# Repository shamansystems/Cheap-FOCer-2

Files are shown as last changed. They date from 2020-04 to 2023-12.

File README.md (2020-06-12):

# Cheap FOCer 2 (v0.9)

Low-Cost(around $120 for 5 boards and components) Motor Controller based on the VESC 6

Front and Back:

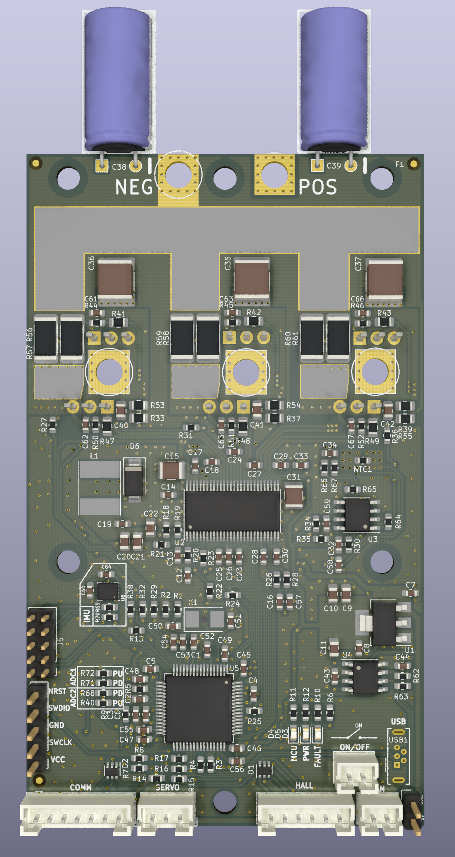
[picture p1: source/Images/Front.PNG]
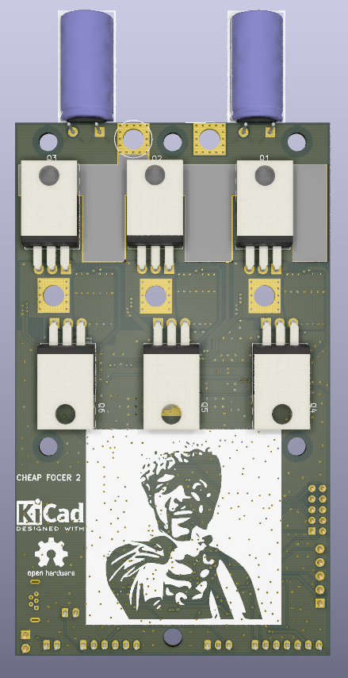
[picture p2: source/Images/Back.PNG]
 

Pin outs:
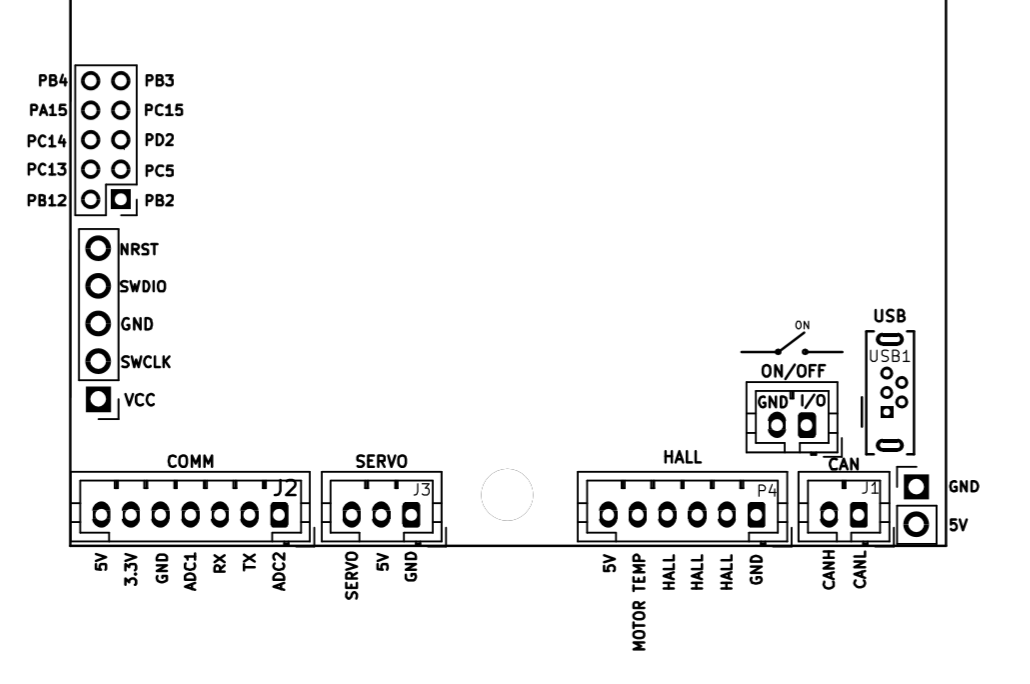
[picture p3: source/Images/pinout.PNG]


## [Support Thread](https://forum.esk8.news/t/cheap-focer-2-open-source-low-cost-vesc-6-based-esc-prototyped-materials-arrived-for-test-batch/13631/1)

## Guides

* [Ordering Guide](./guides/ordering/readme.md)
* [Assembly Guide](./guides/assembly/readme.md)

## Capabilities

* 35A continuous and 70A peak with good heat sinking. These are real values. Not marketing numbers

* Up to 50.4V(12s) safe operating voltage.  For 20s version take a look at [these FOCers](https://forum.esk8.news/t/some-new-focers-84v-vesc-6-based-controllers/1513).

* Compatible with the VESC Tool for configuration

* Open source enclosure design to come

* “Living” LCSC BOM to come. BOM document to be continuously updated with compatible and stocked components from LCSC

## Advantages over VESC 6

* Significantly lower build and BOM cost

* TO-220 FETs allow for big heat sink attachment for better thermal performance

* 2-layer PCB that enables low-cost manufacturing from JLCPCB

* Designed with JLCPCB’s SMT assembly service in mind

* Added optional ON/OFF connector to turn off control circuitry when controller is not in use

* CAN connector changed to 2-pin to avoid improper connections that can cause damage

* ESD protected I/O

* Hardware open sourced

* Designed with direct meme integration

## Advantages over Cheap FOCer 1

* VESC 6 based instead of VESC 4.12

* Significantly improved layout to reduce current loops and facilitate low-noise operation of both the power stage and control circuitry for more stable operation

* Has IMU for balancing applications

* Lower profile

* Handles lower inductance motors much better

* All components on the top side except MOSFETs

* Addition of JST connectors to replace pin headers for Servo, CAN, COMM, ect.

* Addition of header for unused GPIO pins

* Micro USB

## Disadvantages (that I know of)

* Larger than original VESC 6. Cheap FOCer 2 is about 60mm x 100mm x 14mm without enclosure/heat sink

* Uses custom firmware that’s not currently supported in the VESC project. Will make firmware available on GitHub until Cheap FOCer 2 is added to and supported by the official VESC project.

## Kown Issues

* :warning: **Potential Issue with SMT Assembly of the DRV8301 from JLCPCB**

A few have reported blown up D1 diode arrays upon initial powering on of the CFOC2. The issue has been discovered to be inadequate soldering of the DRV which leads to an unregulated 5V of which could actually be 7V or greater. This doesn't happen with every unit and seems to be intermittent. 

**It is recommended that you reflow the DRV and/or touch up the soldering of both the legs and the large pad underneath before initial power on.**

The potential cause of this is the small hole in the DRV's ground pad that was meant to allow soldering of the DRV with even a normal iron (like the CFOC1). This will be removed in the CFOC2 v1.0 release and the pad returned to a normal SMD pad. 

## Warning

* The Cheap FOCer 2 has been bench tested but is still being field tested. Hardware or firmware flaws could still exist and affect user operation.
* You are liable for any and all controllers built using this design. This product is intended for hobbyists and not intended for commercial use.

## License

Cheap FOCer 2 is licensed under the Creative Commons Attribution-ShareAlike 4.0 International License. To view a copy of this license, visit <http://creativecommons.org/licenses/by-sa/4.0/.>

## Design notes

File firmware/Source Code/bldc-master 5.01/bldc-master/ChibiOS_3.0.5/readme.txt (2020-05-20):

*****************************************************************************
*** Files Organization                                                    ***
*****************************************************************************

--{root}                  - ChibiOS/RT directory.
  +--readme.txt           - This file.
  +--documentation.html   - Shortcut to the web documentation page.
  +--license.txt          - GPL license text.
  +--exception.txt        - GPL exception text (stable releases only).
  +--demos/               - Demo projects, one directory per platform.
  +--docs/                - Documentation.
  |  +--common/           - Documentation common build resources.
  |  +--hal/              - Builders for HAL.
  |  |  +--Doxyfile_*     - Doxygen project files (required for rebuild).
  |  |  +--html/          - Local HTML documentation (after rebuild).
  |  |  +--reports/       - Test reports.
  |  |  +--rsc/           - Documentation resource files (required for rebuild).
  |  |  +--src/           - Documentation source files (required for rebuild).
  |  |  +--Doxyfile_*     - Doxygen project files (required for rebuild).
  |  |  +--index.html     - Local documentation access (after rebuild).
  |  +--nil/              - Builders for NIL.
  |  |  +--Doxyfile_*     - Doxygen project files (required for rebuild).
  |  |  +--html/          - Local HTML documentation (after rebuild).
  |  |  +--reports/       - Test reports.
  |  |  +--rsc/           - Documentation resource files (required for rebuild).
  |  |  +--src/           - Documentation source files (required for rebuild).
  |  |  +--Doxyfile_*     - Doxygen project files (required for rebuild).
  |  |  +--index.html     - Local documentation access (after rebuild).
  |  +--rt/               - Builders for RT.
  |  |  +--html/          - Local HTML documentation (after rebuild).
  |  |  +--reports/       - Test reports.
  |  |  +--rsc/           - Documentation resource files (required for rebuild).
  |  |  +--src/           - Documentation source files (required for rebuild).
  |  |  +--Doxyfile_*     - Doxygen project files (required for rebuild).
  |  |  +--index.html     - Local documentation access (after rebuild).
  +--ext/                 - External libraries, not part of ChibiOS/RT.
  +--os/                  - ChibiOS components.
  |  +--hal/              - HAL component.
  |  |  +--boards/        - HAL board support files.
  |  |  +--dox/           - HAL documentation resources.
  |  |  +--include/       - HAL high level headers.
  |  |  +--lib/           - HAL libraries.
  |  |  +--osal/          - HAL OSAL implementations.
  |  |  +--src/           - HAL high level source.
  |  |  +--ports/         - HAL ports.
  |  |  +--templates/     - HAL driver template files.
  |  |     +--osal/       - HAL OSAL templates.
  |  +--nil/              - NIL RTOS component.
  |  |  +--dox/           - NIL documentation resources.
  |  |  +--include/       - NIL high level headers.
  |  |  +--src/           - NIL high level source.
  |  |  +--ports/         - NIL ports.
  |  |  +--templates/     - NIL port template files.
  |  +--rt/               - RT RTOS component.
  |  |  +--dox/           - RT documentation resources.
  |  |  +--include/       - RT high level headers.
  |  |  +--src/           - RT high level source.
  |  |  +--ports/         - RT ports.
  |  |  +--templates/     - RT port template files.
  |  +--various/          - Various portable support files.
  +--test/                - Kernel test suite source code.
  |  +--lib/              - Portable test engine.
  |  +--hal/              - HAL test suites.
  |  |  +--testbuild/     - HAL uild test and MISRA check.
  |  +--nil/              - NIL test suites.
  |  |  +--testbuild/     - NIL nuild test and MISRA check.
  |  +--rt/               - RT test suites.
  |  |  +--testbuild/     - RT build test and MISRA check.
  |  |  +--coverage/      - RT code coverage project.
  +--testhal/             - HAL integration test demos.

*****************************************************************************
*** Releases and Change Log                                               ***
*****************************************************************************

*** 3.0.5 ***
- VAR: Fixed missing time convesion in lwIP arch module (bug #696).
- NIL: NIL_CFG_USE_EVENTS not properly checked in NIL (bug #694).
- RT:  Fixed ISR statistics are not updated from a critical zone in RT
       (bug #693).
- NIL: Fixed NIL test suite calls I and S functions outside critical zone
       (bug #692).
- NIL: Fixed protocol violation in NIL OSAL (bug #691).
- HAL: Fixed STM32 CAN driver always broadcasts tx complete for mailbox 1
       (bug #690).
- RT:  Fixed tm_stop - best case bug (bug #688).
- RT:  Fixed ARM port enforcing THUMB mode (bug #687).
- HAL: Fixed HAL drivers still calling RT functions (bug #686).
- HAL: Fixed Serial_USB improperly resets queues on stop (bug #685).
- HAL: Fixed chprintf() still calling RT functions (bug #684).
- ALL: Several minor documentation/formatting-related fixes.

*** 3.0.4 ***
- HAL: Fixed STM32 ICU driver uses chSysLock and chSysUnlock (bug #681).
- HAL: Fixed wrong DMA priority assigned to STM32F3 ADC3&4 (bug #680).
- HAL: Fixed invalid DMA settings in STM32 DACv1 driver in dual mode
      (bug #677).
- HAL: Fixed usbStop() hangs in STM32 OTGv1 driver (bug #674).
- HAL: Fixed STM32 I2Cv2 driver fails on transfers greater than 255 bytes
       (bug #673).
- HAL: Fixed STM32 I2Cv2 DMA conflict (bug #671).
- HAL: Fixed invalid macro in STM32F0xx registry (bug #668).
- HAL: Fixed I2S clock selection not working in STM32F4xx HAL (bug #667).
- HAL: Fixed STM32 USBv1 broken isochronous endpoints (bug #662).
- HAL: Fixed STM32 USBv1 wrong multiplier when calculating descriptor address
       in BTABLE (bug #661).
- HAL: Fixed STM32 USBv1 does not make use of BTABLE_ADDR define(bug #660).

*** 3.0.3 ***
- HAL: Fixed differences in STM32F3 ADC macro definitions (bug #665).
- HAL: Fixed RTC module loses day of week when converting (bug #664).
- HAL: Fixed invalid class type for sdPutWouldBlock() and sdGetWouldBlock()
       functions (bug #659).
- HAL: Fixed STM32L1xx HAL errors in comments (bug #657).
- HAL: Fixed STM32 USBv1 wrong buffer alignment (bug #656).
- HAL: Fixed Wrong vector name for STM32F3xx EXTI33 (bug #655).
- HAL: Fixed nvicEnableVector broken for Cortex-M0 (bug #654).
- HAL: Fixed missing RCC and ISR definitions for STM32F0xx timers (bug #651).
- HAL: Fixed incorrect compiler check in STM32 RTCv1 driver (bug #650).
- HAL: Fixed STM32F3xx HAL checking for non-existing macros (bug #648).
- HAL: Fixed error in STM32F030 EXT driver (bug #647).
- RT:  Fixed problem with chTimeIsWithin() (bug #646).
- VAR: Fixed _sbrk_r with incr == 0 should be valid (bug #645).
- RT:  Fixed issues in CMSIS RTOS interface (bug #644).
- HAL: Fixed rtcConvertDateTimeToFAT() incorrect conversion (bug #615).

*** 3.0.2 ***
- HAL: Fixed RT dependency in STM32 SDCv1 driver (bug #643).
- VAR: Fixed incorrect working area size in LwIP creation in demos (bug #642).
- HAL: Fixed error in hal_lld_f100.h checks (bug #641).
- HAL: Fixed volatile variable issue in I/O queues, both RT and HAL (bug #640).
- HAL: Fixed wrong DMA assignment for I2C1 in STM32F302xC registry (bug #637).
- HAL: Fixed missing timers 5, 6, 7, 10 & 11 from STM32L1 HAL port (bug #636).
- VAR: Fixed CRT0_CALL_DESTRUCTORS not utilized in crt0_v7m.s (bug #635).
- DEM: Fixed wrong ld file in STM32F072xB USB CDC demo (bug #634).
- NIL: Fixed wrong assertion in NIL chSemResetI() and NIL OSAL
       osalThreadDequeueAllI() (bug #633).
- RT:  Fixed problem with RT mutexes involving priority inheritance (bug #632).
- HAL: Fixed HAL to RT dependency in STM32 DAC driver (bug #631).
- HAL: Fixed problem with STM32 I2S driver restart (bug #630).
- NIL: Added polled delays required to fix bug #629.
- HAL: Fixed STM32F3xx ADC driver uses US2RTC directly (bug #629).

*** 3.0.1 ***
- HAL: Fixed CEC clock cannot be disabled on STM32F0xx (bug #628).
- VAR: Fixed lwIP arch code breaks with a 16-bit systick timer (bug #627).
- HAL: Fixed broken MAC driver for STM32F107 (bug #626).
- NIL: Fixed missing configuration options from NIL PPC port (bug #625).
- HAL: Fixed wrong offset in STM32 DAC driver (bug #624).
- HAL: Fixed crash on STM32F030x4/6 devices (bug #623).
- HAL: Fixed duplicated doxygen tag in STM32F4xx hal_lld.h file (bug #621).
- HAL: Fixed STM32F042 registry error (bug #620).
- HAL: Fixed wrong check in canReceive() (bug #619).
- HAL: Fixed wrong EXTI[18] vector number on STM32F373 (bug #618).
- HAL: Fixed wrong check on STM32_LSE_ENABLED definition in STM32L1xx HAL port
       (bug #617).

*** 3.0.0 ***
- NEW: Added an initialization function to the lwIP bindings, now it is
       sufficient to call lwipInit(NULL); in order to start the subsystem.
       Demo updated.
- RT:  Fixed compilation error in RT when registry is disabled (bug #614).
- NIL: Fixed OSAL_ST_MODE not defined in AVR port (bug #613).
- NIL: Fixed nilrtos redefinition of systime_t (bug #611).
- HAL: Fixed TIM2 wrongly classified as 32bits in STM32F1xx devices
       (bug #610).

*** 3.0.0p6 ***
- HAL: Removed call to localtime_r() function for non-GNU compilers in
       STM32F1xx RTC driver.
- DEM: Fixed the FatFS demo timeout, now it is expressed in milliseconds.
- DEM: Added -Wundef to all the demos and test programs in order to find
       common error cases.
- NIL: Added INTC priorities check to the e200z port.
- RT:  Added INTC priorities check to the e200z port.
- HAL: Added support for CAN in STM32F042/72 devices.
- HAL: Added support for extra DMA channels in STM32F072 devices.
- HAL: Modified the STM32 CAN driver to support unified IRQs.
- RT:  SPE-related issue in e200z ports (bug #607).
- NIL: SPE-related issue in e200z ports (bug #607).
- HAL: Fixed dependency between STM32 MAC driver and RT (bug #606).
- HAL: Fixed wrong macro names in STM32F0xx HAL driver (bug #605).
- HAL: Fixed wrong check on ADC3 in STM32F3xx ADC driver (bug #604).
- HAL: Fixed wrong macro names in STM32F3xx HAL driver (bug #603).
- HAL: Fixed errors in STM32 OTGv1 driver (bug #601).
- DEM: Fixed missing paths in e200z demos (bug #600).
- HAL: Fixed error in platform_f105_f107.mk file (bug #599).
- HAL: Fixed issue in DMA drivers when channels share ISRs (bug #597).

*** 3.0.0p5 ***
- HAL: Added no-DMA mode to the STM32 I2Cv2 driver.
- HAL: Added DAC support to all STM32 sub-platforms, added another demo for
       the STM32F3xx.
- HAL: Fixed STM32 USARTv1: incorrect txend2_cb callback behavior (bug #596).
- DEM: Fixed wrong comment in ARMCM4-STM32F401RE-NUCLEO demo (bug #595).
- HAL: Fixed STM32 SDC LLD driver initialization with Asserts disabled
       (bug #594).

*** 3.0.0p4 ***
- NEW: Added no-DMA mode to STM32 I2Cv2 driver.
- BLD: New "smart build" mode added to makefiles, now only used files are
       compiled.
- HAL: Change to the Serial_USB driver, now the INT endpoint is no more
       mandatory.
- HAL: New DAC driver implementation for STM32F4xx.
- HAL: Fixed SDC STM32 driver broken in 50MHz mode (bug #592).
- HAL: Fixed STM32 RTC SSR Register Counts Down (bug #591).
- HAL: Fixed STM32 RTC PRER Register not being set in init (bug #590).
- HAL: Fixed STM32F334 does not have an EXT18 interrupt (bug #588).
- HAL: Fixed STM32L1xx USB is missing disconnect/connect macros (bug #587).
- HAL: Fixed wrong vector number for STM32L1xx USB (bug #586).
- HAL: Fixed spurious TC interrupt in STM32 UART (v1 and v2) driver (bug #584).
- HAL: Fixed invalid checks on STM32L1xx LSI and LSE clocks (bug #583).
- HAL: Fixed RCC CAN2 macros missing in STM32F1xx platform (bug #582).
- HAL: Fixed STM32 I2Cv2 driver issue (bug 581).
- BLD: Fixed ules.mk: adding "PRE_MAKE_ALL_RULE_HOOK" (bug #580).
- BLD: Fixed rules.mk should not explicitly depend on $(BUILDDIR) (bug #579).

*** 3.0.0p3 ***
- RT:  Fixed tickless mode instability in RT (bug 577).

*** 3.0.0p2 ***
- HAL: Fixed instances of RT API in HAL drivers (bug 574).
- RT:  Fixed system time overflow issue in tickless mode (bug 573).
- RT:  Improvements to the IRQ_STORM applications.

*** 3.0.0p1 ***
- First 3.0.0 release, see release note 3.0.0.

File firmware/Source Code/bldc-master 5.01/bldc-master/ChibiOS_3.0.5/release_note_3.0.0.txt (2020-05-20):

ChibiOS 3.0 is now composed of several independent but inter-operable sub-projects: RT, NIL, HAL.

ChibiOS 3.0 general highlights

- New files tree organization makes the system more modular.
- A community-contributed code area is now part of the files architecture, it will allow for easier integration of contributed code without much screening.
- Improved startup files, scatter files and build system.
- New licensing options.
- Free ChibiStudio IDE support.

What's new in RT 3.0

- MISRA 2012 compliant.
- Entirely static for enhanced safety.
- System data is now encapsulated in a single "ch" global structure for enhanced safety.
- System integrity check runtime functionality for enhanced safety.
- Tick-less kernel mode helps implement ultra-low-power devices.
- High Resolution Virtual Timers module allows to specify very short intervals.
- High Resolution system time.
- Clock-cycle accurate Time Measurement module.
- Clock-cycle accurate polled delays.
- Statistic module provides high resolution measurement of threads, ISRs and critical zones.
- New recursive locks in addition to the classical critical zone primitives.
- New recursive mode for Mutexes.
- Enhanced suspend/resume mechanism for threads.
- CMSIS-compliant ARM Cortex-Mx port.
- CMSIS RTOS API available.
- Multi-compilers architecture for ports.
- Codebase now compatible with GCC link time optimizations.

What's new in HAL 3.0

- MISRA 2012 compliant.
- HAL is now entirely licensed under Apache 2.0 license.
- HAL has been decoupled from RT. It can now be adapted to any reasonable RTOS or even used with no RTOS at all thanks to a new abstraction layer named OSAL. OSAL implementations are provided for RT, NIL, bare metal ARM Cortex-Mx cores, bare metal Power e200z cores.
- New driver models for ST, I2S, DAC.
- Revamped ADC, ICU, PWM, RTC, SDC, USB drivers.
- Greatly improved STM32 family support, all sub-families have been added.
- Support for new families expanding (Kinetis, Tiva, SPC5xx, RL78, RX62N).
- Streams, channels, files and block devices abstract interfaces.

New addition NIL 1.0

- MISRA 2012 compliant.
- Entirely static for enhanced safety.
- No linked lists anywhere in the code for enhanced safety.
- System data is encapsulated in a single "nil" global structure for enhanced safety.
- Tick-less kernel mode helps implement ultra-low-power devices.
- Ultra compact kernel, well below 1kB in its maximum configuration.
- Upward compatible with RT, it implements a subset of the RT API.
- Reduced RAM usage, 20-28 bytes for task and just 4 bytes for a semaphore on 32 bits architectures, half of that on 8/16 bits architectures.
- ARM Cortex-Mx port based on CMSIS architecture.
- Multi-compilers architecture for ports.

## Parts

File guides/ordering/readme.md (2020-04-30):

# JLCPCB and LCSC Ordering Guide

## JLCPCB

1. Clone or [download](https://github.com/shamansystems/Cheap-FOCer-2/archive/master.zip) the Cheap FOCer 2 repository and have the files available

1. [Create an account](https://passport.easyeda.com/register) with [JLCPCB.com](http://JLCPCB.com). This account will also carry over to [LCSC.com](http://LCSC.com) since they are the same company.

1. Go to: [https://cart.jlcpcb.com/quote](https://cart.jlcpcb.com/quote)

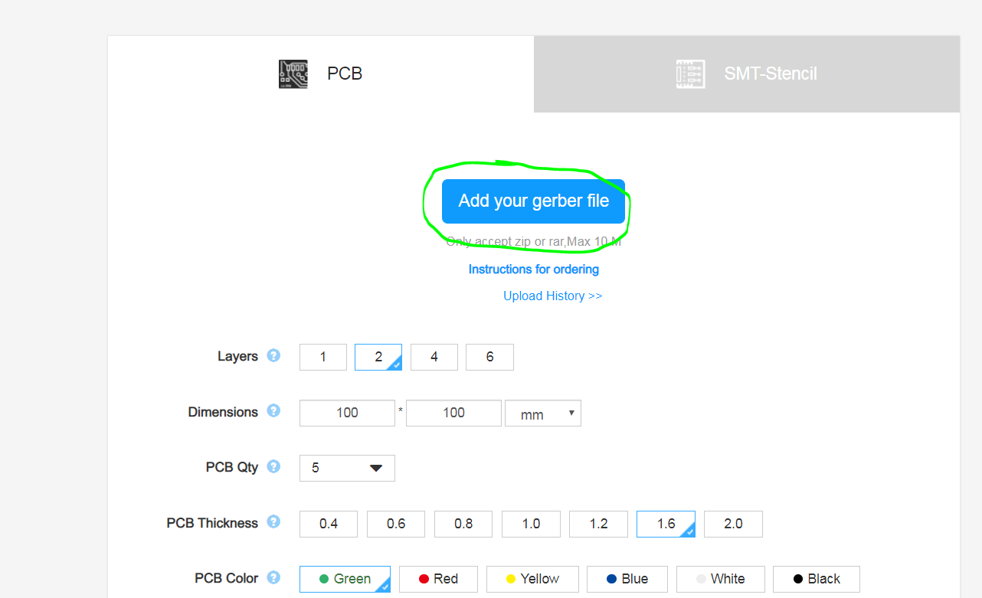
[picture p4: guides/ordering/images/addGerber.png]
1. Click the `Add your gerber file` button and select the [gerber.zip](../../gerber.zip) file from the root directory 

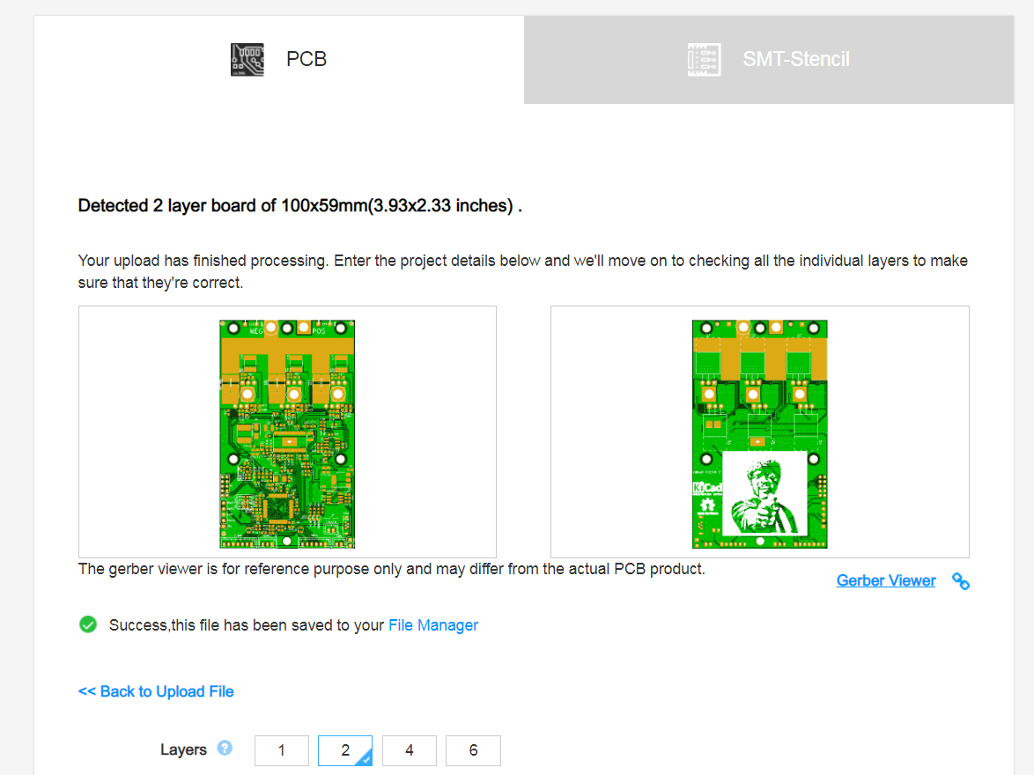
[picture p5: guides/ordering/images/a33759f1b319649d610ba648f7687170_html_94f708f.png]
1. You should now see the CFOC2 front and back in the preview as shown below 

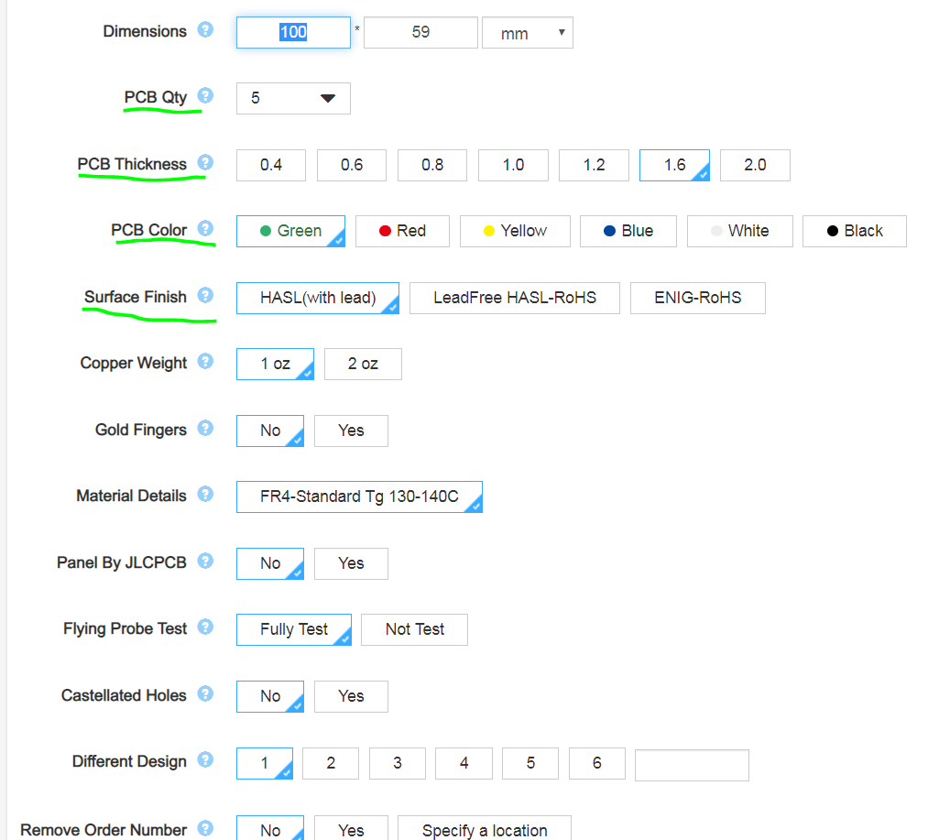
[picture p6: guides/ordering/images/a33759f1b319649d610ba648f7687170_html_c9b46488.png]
1. There are a few properties that you can customize if you want. The PCB quantity (the amount you want made), thickness, color, and surface finish are all I recommend adjusting to preference. Note that certain choices of these options will affect pricing. By default, the cheapest options are already selected. 

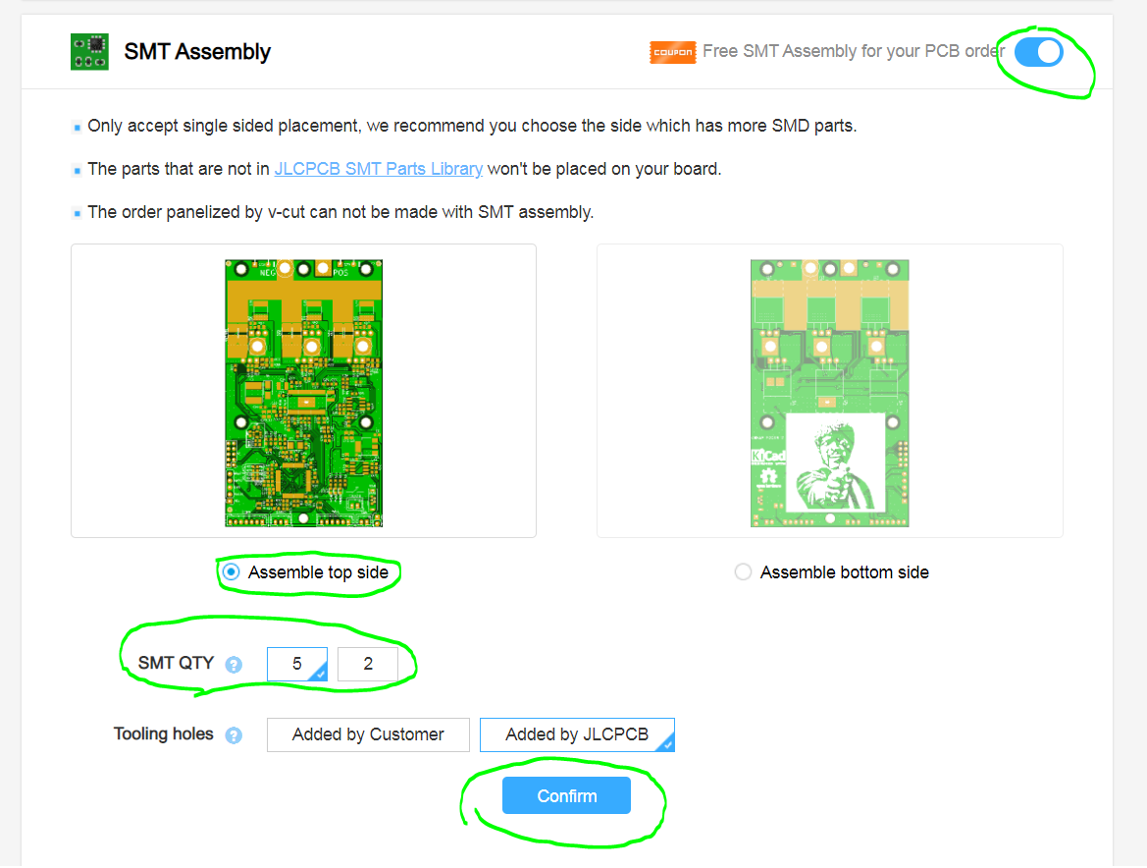
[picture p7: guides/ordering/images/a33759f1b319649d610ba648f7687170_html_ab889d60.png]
1. Select the toggle button to enable SMT Assembly 

1. Select the `Assemble top side` option

1. Select how many boards you want assembled with the `SMT QTY` option

1. Select the `confirm` button to continue

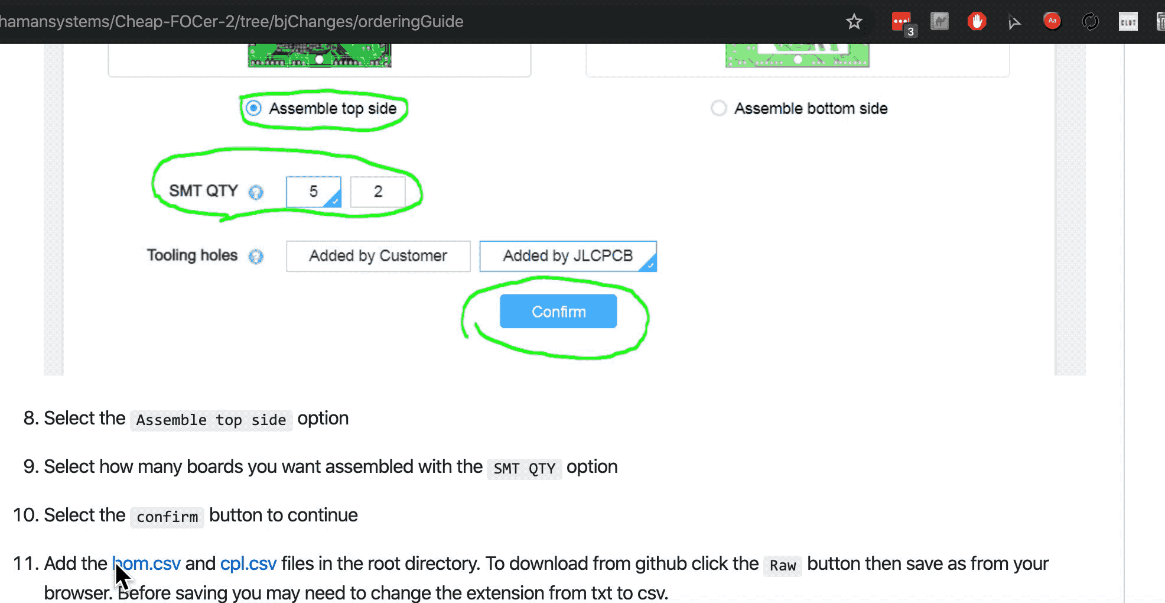
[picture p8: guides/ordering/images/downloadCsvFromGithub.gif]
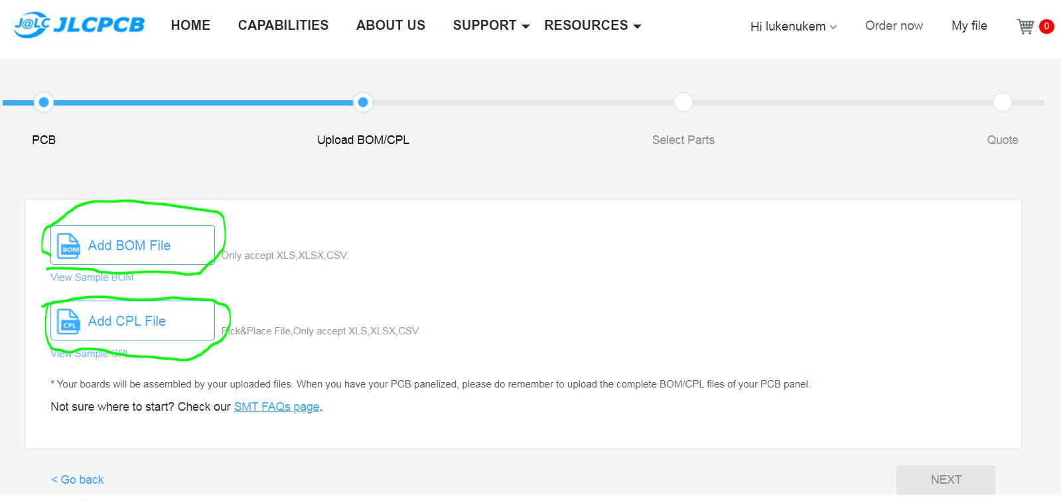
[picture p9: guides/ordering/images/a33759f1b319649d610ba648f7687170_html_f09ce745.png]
1. Add the [bom.csv](../../bom.csv) and [cpl.csv](../../cpl.csv) files in the root directory.  To download from github click the `Raw` button then save as from your browser.  Before saving you may need to change the extension from txt to csv.  

1. Click `Next` to continue

1.
    You will now see the parts selected by JLCPCB based on the BOM that was uploaded. This list of parts includes every possible component available by JLCPCB to be assemble onto the Cheap FOCer 2.

    The `Extended Parts` such as the DRV8301 and the 100v rated components cost more but will be much better if JLCPCB solders it for you.  The DRV8301 chip is one of the hardest things to solder by hand.

    The only parts that you should see as `No part selected` are the (10uF, 100V) caps, the 22uH inductor, the BMI160 IMU, and the (4.7uF, 100V) caps. These components plus the MOSFETs must be acquired and assembled external to JLCPCB. Ordering these remaining components from LCSC.com will be covered [later in this guide](#remaining-components-from-lcsccom).
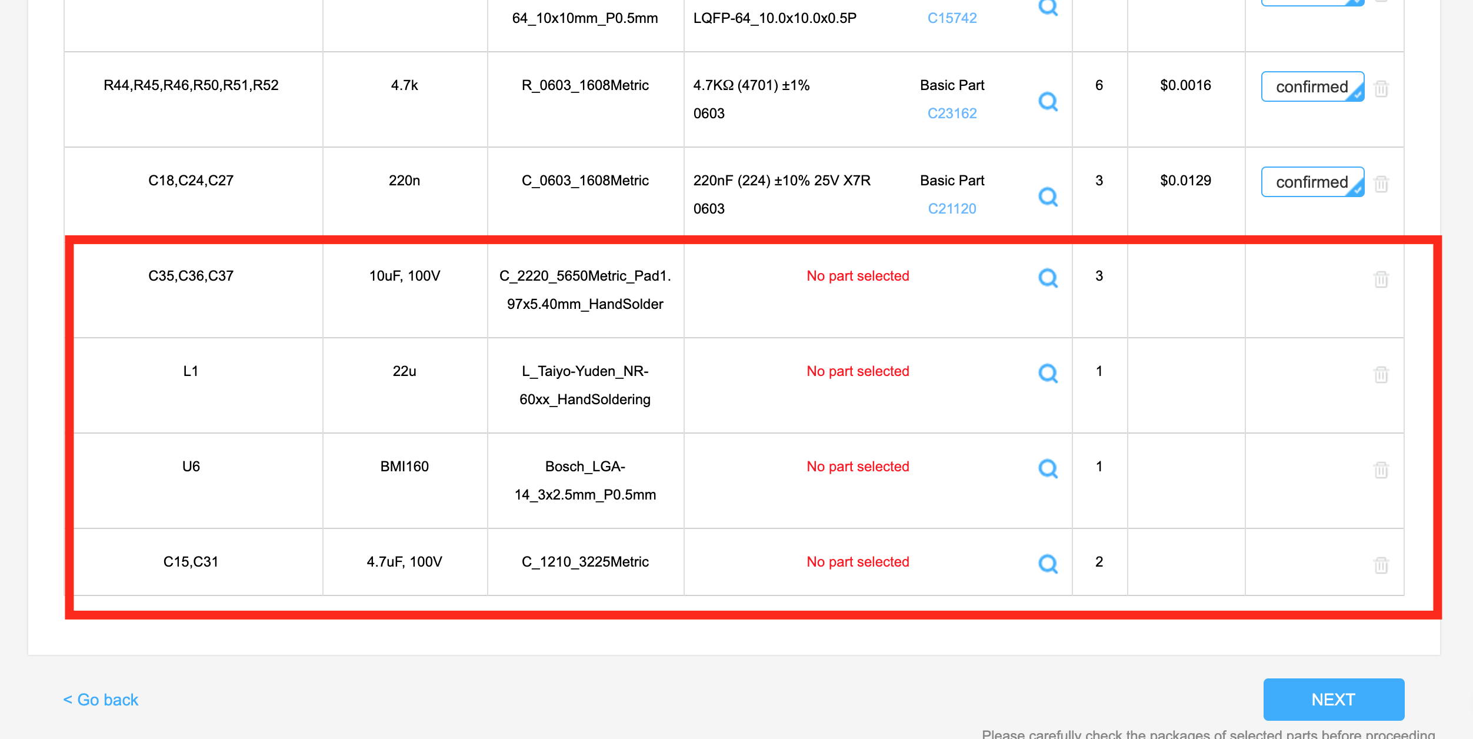
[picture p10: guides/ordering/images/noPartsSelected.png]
    

    If you intend to use your FOCer for balancing applications such as a onewheel or unicycle you will have to solder the BMI160 IMU yourself. This is a leadless component which requires a [reflow station](https://www.aliexpress.com/item/32747661606.html).

    If you have components that are **out of stock** or discontinued please see [this note](#out-of-stock-or-discontinued-components) below.

1. Click `Next` to continue

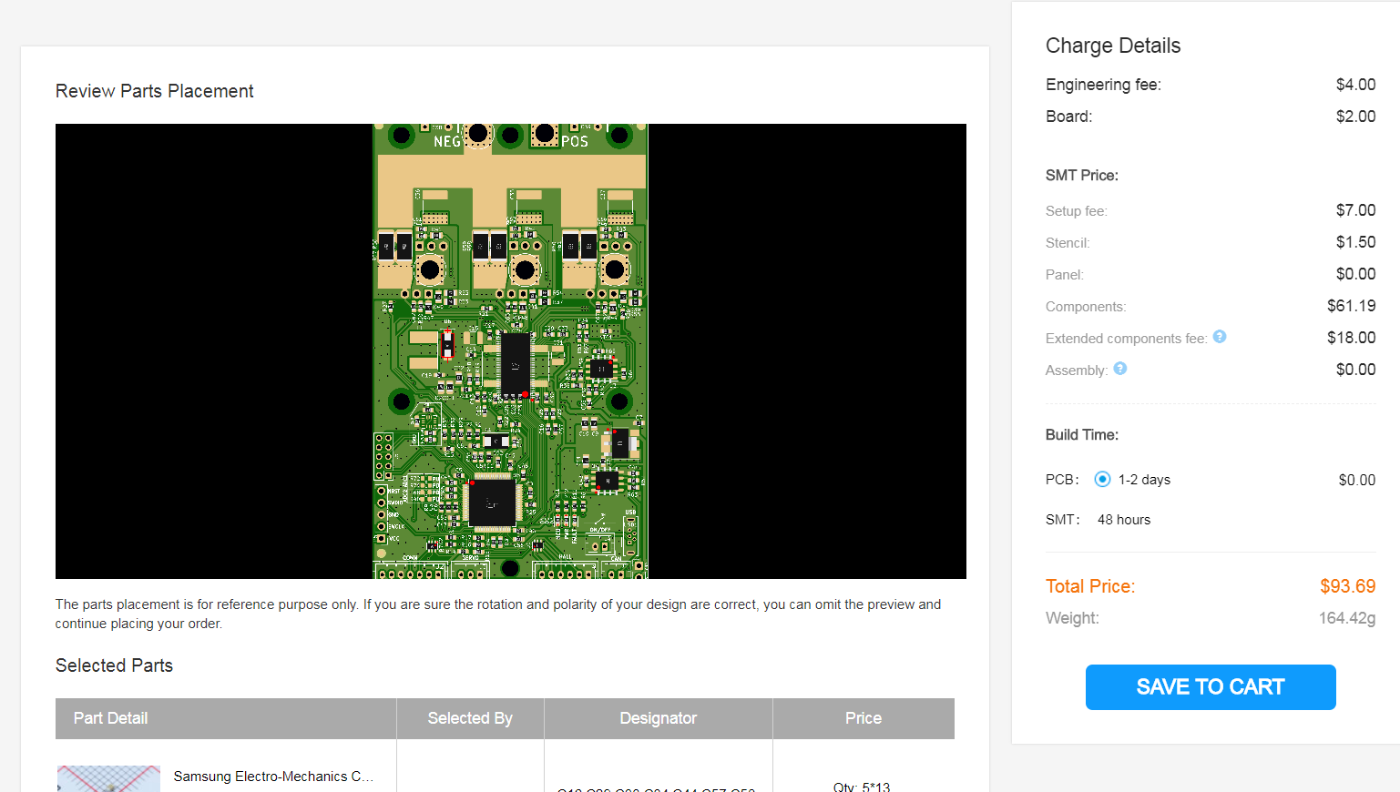
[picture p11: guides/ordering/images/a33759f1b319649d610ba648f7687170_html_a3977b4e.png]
1. You should now see a preview of the parts placement on the CFOC2. The placement of the DRV8301 and a few other multi-pin components will appear wrongly placed. **This is ok.** JLCPCB will correct this later in what they call a `DFM review`. I have had no issues in letting JLCPCB handle the correction of component placement in all of my many orders. 

1.
    Scroll down and you will see a list of `Unselected Parts`. The [LCSC BOM file](../../5XBomLcsc.csv) covered [later in this guide](#remaining-components-from-lcsccom) will fulfill the remaining parts.
    

    If you excluded certain parts on your own or if JLCPCB was out of stock of something, then click the `Download Unselected Parts List` button for a list of what you will need to acquire outside of this guide.

1. Next click `Save to Cart` and proceed through the checkout process. If you’ve made it this far then congratulations! The hardest part is over and we will now proceed to ordering the remaining components from LCSC.com.

## Remaining Components from [LCSC.com](http://lcsc.com)

1. Go to [LCSC's boom tool](https://lcsc.com/bom.html#/upload)

1. Click `select a file` and upload [5XBomLcsc.csv](../../5XBomLcsc.csv)


1. There should now be a list that has loaded on your screen. You will need to select the column header the `Quantity` and `Manufacture Part Number` columns from the drop-down menus as shown below.
    

1. Click `Next` to continue.

1. You should now see a page showing the parts that LCSC has chosen to fit the parts described in the BOM that was uploaded. Scroll through the list to verify that all parts are present and accounted for. Notice that certain components, have a minimum order quantities and you will need to update the quantities of these items to meet the minimum requirements
    

1. Quantities of parts in this list are for 5 CFOC2. Please scale up the quantities per amount of CFOC2 PCBs you have ordered from JLCPCB.
1. If this is your first time be sure to order extra parts incase you make a mistake

1. If you have components that are **out of stock** or discontinued please see [this note](#out-of-stock-or-discontinued-components) below.

1. After settling on the quantities you want, please add items to your cart and proceed with the checkout process.

1. Next check out the prerequisites section of the [assembly guide](../assembly/) to prepare for when your PCB arrives

## Out of Stock or Discontinued Components

Please note that JLCPCB and LCSC will often run out of stock on certain components. There is a chance you may have to find an alternative component with the same footprint and properties. Check [this page](outOfStock.md) to see if there are alternatives listed for your part.  If not, post a [github issue](https://github.com/shamansystems/Cheap-FOCer-2/issues) of where you found a new part so that others can see and we can update [this page](outOfStock.md).

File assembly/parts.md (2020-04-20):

# Parts List
1. PCB with basic parts placed and soldered from PCB manufacture.  Follow [this guide](../orderingGuide/readme.md). 

1. Soldering Iron.  
Suggestions:
    * https://www.amazon.com/X-Tronic-3020-XTS-Digital-Display-Soldering/dp/B01DGZFSNE

## Optional Parts
* [reflow station with soldering iron](https://www.amazon.com/Flexzion-Digital-Soldering-Station-Desoldering/dp/B0154G4A28)

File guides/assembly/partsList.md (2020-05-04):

# Parts

### AliExpress Wishlist

Wishlist for 5 FOCers: [AliExpress](https://my.aliexpress.com/wishlist/shared.htm?groupId=100000021433489)

### **SMD Assembled PCB**

* Follow **[this guide](../ordering/readme.md)**
* 1 per FOCer

### **Heat Sink**: [AliExpress](https://www.AliExpress.com/item/32951112852.html)

* 60mm x 100mm ( x 10mm) flat surface [Heat sink](images/heatSink.jpeg)
* 1 per FOCer
* Any [generic heat sink](images/heatSink.jpeg) with a flat surface of at least 60mm x 100mm can be used

### **Thermal Pad**: [AliExpress](https://www.AliExpress.com/item/32810504639.html)

* 60mm x 60mm x 1mm non conductive [Thermal pad](images/thermalPad.jpeg)
* 1 per FOCer
* This electrically insulates the MOSFET tabs from the heat sink (very important).
* 0.5mm thick thermal pad **will NOT be sufficient** to fill the gap between MOSFET tabs and heat sink surface.

### **Thermal Paste**: [AliExpress](https://www.aliexpress.com/item/4000082981600.html)

* Any Thermal Paste
* 2 dabs per FOCer
* Yes you need both pads and paste
* Paste is used to help connect a MOSFET to the thermocouple

### **Screws**: [AliExpress](https://www.aliexpress.com/item/32966917947.html)

* m3 x 12mm hex button head [screws](images/screws.jpg)
* 6 per FOCer

### **Thread Lock**: [AliExpress](https://www.aliexpress.com/item/4000015095892.html)

* To keep screws in while being vibrated

### **Spacers**: [AliExpress](https://www.AliExpress.com/item/33047891996.html),  [Ebay](https://www.ebay.com/itm/OD7-5mm-Nylon-Round-Spacer-Standoff-For-M3-thread-Screw-Blot-QTY50/183743008473), [Thingiverse](https://www.thingiverse.com/thing:4332442)

* M3/M4 5mm nylon [spacers](images/spacers.jpeg)
* 6 per FOCer
* Spacers to prevent over-tightening of screws, which cause warping/damage to the PCB.
* **If printing**, use PETG or ABS as PLA warps at around 60c

### **Washers**: [AliExpress](https://www.AliExpress.com/item/33021883302.html) [Thingiverse](https://www.thingiverse.com/thing:4332442)

* M3 x 6mm x 1 mm Nylon [Washers](images/washers.jpeg)
* 6 per FOCer

## Optional Parts

### **Pin Headers**:  [AliExpress](https://www.AliExpress.com/item/4000909558952.html)

* [Pin headers](pinHeaders.png)
* A pack of 10 should do for 5 boards
* Used for GPIO and the initial bootloader/firmware flashing

### **Power Switch**: [AliExpress](https://www.AliExpress.com/item/4000358463924.html)

* 2 position switch
* 1 per FOCer
* just need to open/close the circuit

### **Fan**: [AliExpress](https://www.AliExpress.com/item/32571979071.html)

* 60 MM 5v [Fan](images/fan.jpeg)
* 1 per FOCer
* Can be mounted to Heat Sink Fins to provide additional cooling potential.

### **Power Adapter**: [AliExpress](https://www.aliexpress.com/item/32873131460.html)

* Used to test newly assembled FOCer
* 5v minimum
* 100mA/.1 amp so that you can minimize potential damage to improperly assembled FOCer

### **Case**: [Thingiverse](https://www.thingiverse.com/thing:4332442)
* 1 per FOCer

## Wires, Cables and Connectors

### **Battery & Motor Phase Wire**: [AliExpress](https://www.AliExpress.com/item/33057076463.html)

* 100mm of 12AWG or 10AWG Silicone Stranded Wire
* 1 red & 4 black(500mm total) per FOCer
* [The shorter the better on the battery side](https://www.youtube.com/watch?v=54bb9zpDdZU)

### **Battery Connector**: [AliExpress](https://www.AliExpress.com/item/32546847748.html)

* XT60 or XT90 [male](images/xt90MvF.jpg) **Amass** connector
* 1 per FOCer

### **Motor Connectors**: [AliExpress](https://www.AliExpress.com/item/32926203705.html)

* 4mm female bullet connectors
* 3 per FOCer
* Other options: 4.5mm/5mm/5.5mm/etc. bullet connectors, [MT60](https://www.aliexpress.com/item/32801541697.html)

### **Pigtails**: [AliExpress](https://www.AliExpress.com/item/32733307616.html)

* JST PH 2.0 Pigtails
* 2x2pin per FOCer
* 1x3pin per FOCer
* 1x6pin per FOCer
* 1x7pin per FOCer

### **Heat Shrink**

* For the PCB(instead of an enclosure) - [AliExpress](https://a.AliExpress.com/_dUNLfKc)
* 70mm diameter for PCBs with heat sink
* For other wires(motor bullet connectors)- [AliExpress](https://www.AliExpress.com/item/33008449230.html)

## Consumables

### **Solder**(required): [AliExpress](https://www.AliExpress.com/item/32946643268.html) [Amazon](https://www.amazon.com/MG-Chemicals-Leaded-Solder-Pocket/dp/B072JQ1N4G)

* 0.5 for smaller parts and 1mm for larger wire
* rosin core

### **Cutting Oil**

* For adding threaded holes to the heat sink
* Could use most any oil you have on hand

### **Solder Wick**: [AliExpress](https://www.aliexpress.com/item/32958719300.html)

* Braided copper solder wick
* 1 roll for the rest of your life, if you don't fuck up too much
* Helps with removing bridges and [small chips](https://youtu.be/8yyUlABj29o)

### **Flux**: [AliExpress](https://www.AliExpress.com/item/32828595199.html)

* One tube should do for 5 or more boards
* Makes soldering work better

## Tools List

### **ST-Link V2** (Required)

* ST-Link V2: [AliExpress](https://www.AliExpress.com/item/32792513237.html)
* 5-pin 2.54mm male header for connecting to the VESC:  [AliExpress](https://www.AliExpress.com/item/4000909558952.html).  You should have already ordered this as part of the [5XBomLcsc.csv](../../5XBomLcsc.csv)
* Used to flash the VESC bootloader as part of the initial setup

### **Drill**(required): [AliExpress](https://www.aliexpress.com/item/4000642467959.html)

* Electric Drill
* To drill holes in the heat sink

### **Drill Bit**(required): [AliExpress](https://www.aliexpress.com/item/32483226736.html),[Amazon](https://www.amazon.com/gp/product/B07ZQGXWGL)

* 2.5mm drill bit
* For heat sink connection

### **M3 Allen Key**(required): [AliExpress](https://www.AliExpress.com/item/32676647238.html)

### **Soldering Iron**(required): [AliExpress](https://www.AliExpress.com/item/4000019437594.html), [Amazon](https://www.amazon.com/X-Tronic-3020-XTS-Digital-Display-Soldering/dp/B01DGZFSNE)

* [How to solder tiny things](https://www.overclockers.com/how-to-solder-tiny-things/)
* How to [video style](https://youtu.be/b9FC9fAlfQE)

### **Tap Wrench**: [AliExpress](https://www.aliexpress.com/item/32788074995.html)

* Can also use a socket or vice grips
* Just need something to hold the tap straight

### **Tap**: [AliExpress](https://www.aliexpress.com/item/4000465103162.html)

* M3 Tap
* For heat sink connection
* Can also use one of your steel screws to create threads in the aluminum

### **Reflow Station**- mandatory for the IMU(BMI160): [AliExpress](https://www.aliexpress.com/item/32747661606.html),[Amazon](https://www.amazon.com/Flexzion-Digital-Soldering-Station-Desoldering/dp/B0154G4A28)

### **Helping Hands**- highly recommended: [AliExpress](https://www.aliexpress.com/item/32974107958.html), [Amazon](https://www.amazon.com/gp/product/B078N9DPQ5)

### **Solder Sucker**: [AliExpress](https://www.aliexpress.com/item/32864628837.html)

* To remove solder
* Easier to use than solder wick, not consumable

### **Multimeter**: [AliExpress](https://www.aliexpress.com/item/33046473408.html)

Cant say where or why, but surely you'll need it for something

### **Magnifier/Microscope**: [AliExpress](https://www.aliexpress.com/item/32816285552.html)

Not sure if the AliExpress one is any good.  Don't get the suction mount.

### **Tweezers**: [AliExpress](https://AliExpress.com/item/33019151832.html)

To place small parts

## Accessories

### **Bluetooth Module**- [AliExpress](https://www.AliExpress.com/item/32833817130.html)

* [How to](https://www.youtube.com/watch?v=PFFiVxFHDM4)
* [More info](https://vesc-project.com/node/234)
* I was able to get a [HM-10 Bluetooth 4.0](https://www.AliExpress.com/item/32888733000.html) working with [Ackmaniac's](http://esk8.news/how-to-ackmaniac-esc-tool/) firmware on my vesc at 9600 baud rate

### **Remote**

TODO: Will any remote work?  What should they look for or avoid?

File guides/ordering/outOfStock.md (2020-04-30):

# List Of Components That Go Out Of Stock And Alternative Sources

## Selecting alternatives

Please note that JLCPCB and LCSC will often run out of stock on certain components. There is a chance you may have to find an alternative component with the same footprint and properties. Check below to see if there are alternatives listed for your part.  If not, post a [github issue](https://github.com/shamansystems/Cheap-FOCer-2/issues) of where you found a new part so that others can see and we can update [this page](outOfStock.md).  

## JST-PH(b2b,b3b,b6b,b7b) connectors

Be sure to get JST-PH not JST-XHP because the pin spacing is different. They look like this:


### Alternative Sources

* <https://www.aliexpress.com/item/32733307616.html?spm=a2g0s.9042311.0.0.7a894c4dYDsoaK>

* <https://www.amazon.com/Pieces-JST-PH-Connector-Female-Header/dp/B07P82QFXD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>
* <https://www.ebay.com/sch/m.html?_ssn=chendongsheng1969&_from=R40&_sacat=0&_nkw=JST-PH&_sop=15>
    * fast shipping
    * wires already connected to males
    * asked if they can create an ad just for us with the exact parts we need.  

## MOSFETs(SE60210GA)

Properties

* N Channel 60V 210A 4V @ 250uA 2.6mΩ @ 20A,10V 300W TO-220 MOSFET RoHS
* <https://datasheet.lcsc.com/szlcsc/1912111437_SINO-IC-SE60210GA_C396088.pdf>

## Alternative MOSFETs

  1. [NCEP60T20](https://lcsc.com/product-detail/MOSFET_Wuxi-NCE-Power-Semiconductor-NCEP60T20_C284868.html)
  1. [SE80160GA20](https://lcsc.com/product-detail/MOSFET_SINO-IC-SE80160GA_C393143.html)

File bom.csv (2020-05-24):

Comment | Designator | Footprint | LCSC Part # | Quantity
330u, 63V | C38, C39 | CP_10x20mm_hor_with_model_brd_edge | C437643 | 2 | Blue highlighted componenets are not avaiable from JLCPCB's SMT service.
2.2u | C5, C8, C19, C25, C26, C28, C30, C45, C46, C47, C48, C49, C53, C54, C55, C56 | C_0603_1608Metric | C23630 | 16
1nF | C16, C29, C33, C34, C44, C57, C58, C61, C62, C63, C65, C66, C67 | C_0603_1608Metric | C1588 | 13
100n | C1, C6, C7, C17, C32, C43, C52, C59, C60, C64 | C_0603_1608Metric | C14663 | 10
0.01uF | C2, C3, C4 | C_0603_1608Metric | C57112 | 3
220n | C18, C24, C27 | C_0603_1608Metric | C21120 | 3
15p | C50, C51 | C_0603_1608Metric | C1644 | 2
6.8n | C12 | C_0603_1608Metric | C1631 | 1
150p | C13 | C_0603_1608Metric | C1594 | 1
15nF | C14 | C_0603_1608Metric | C1596 | 1
22n | C23 | C_0603_1608Metric | C21122 | 1
22uf | C9, C10, C11, C20, C21, C22 | C_0805_2012Metric | C45783 | 6
4.7nF, 100V | C40, C41, C42 | C_0805_2012Metric | C21217 | 3
4.7uF, 100V | C15, C31 | C_1210_3225Metric | C385986 | 2
10uF, 100V | C35, C36, C37 | C_2220_5650Metric_Pad1.97x5.40mm_HandSolder | C153035 | 3
2k2 | R2, R12, R15, R16, R17, R25, R29, R32, R38 | R_0603_1608Metric | C4190 | 9
1k | R24, R26, R28, R30, R66, R67, R69, R70 | R_0603_1608Metric | C21190 | 8
100R | R5, R6, R7, R8, R9, R10, R11 | R_0603_1608Metric | C22775 | 7
10k | R13, R14, R22, R23, R34, R35 | R_0603_1608Metric | C25804 | 6
4.7k | R44, R45, R46, R50, R51, R52 | R_0603_1608Metric | C23162 | 6
39k | R1, R27, R31, R36 | R_0603_1608Metric | C23153 | 4
22R | R3, R4 | R_0603_1608Metric | C23345 | 2
56R | R62, R63 | R_0603_1608Metric | C25196 | 2
20k | R64, R65 | R_0603_1608Metric | C4184 | 2
3.3k | R18 | R_0603_1608Metric | C22978 | 1
220k | R19 | R_0603_1608Metric | C22961 | 1
15k | R20 | R_0603_1608Metric | C22809 | 1
18k | R21 | R_0603_1608Metric | C25810 | 1
10R | R33, R37, R39, R41, R42, R43, R47, R48, R49, R53, R54, R55 | R_0805_2012Metric | C17415 | 12
0.001R | R56, R57, R58, R59, R60, R61 | R_2512_Yageo_big_pads | C76233 | 6
22u | L1 | L_Taiyo-Yuden_NR-60xx_HandSoldering | C266430 | 1
100v, 1A | D6 | D_SMA | C360437 | 1
RED | D3 | LED_0603_1608Metric | C2286 | 1
GRN | D4 | LED_0603_1608Metric | C72043 | 1
BLU | D5 | LED_0603_1608Metric | C72041 | 1
SMF05CT1G | D1, D2 | SOT-363_SC-70-6 | C15879 | 2
BMI160 | U6 | Bosch_LGA-14_3x2.5mm_P0.5mm | C94021 | 1
DRV8301 | U2 | HTSSOP-56-1EP_6.1x14mm_P0.5mm_EP3.61x6.35mm | C98969 | 1
STM32F405RGT6 | U5 | LQFP-64_10x10mm_P0.5mm | C15742 | 1
TP2604-SR | U3 | SOIC-8_3.9x4.9mm_P1.27mm | C126446 | 1
TJA1051T/3/1J | U4 | SOIC-8_3.9x4.9mm_P1.27mm | C38695 | 1
AMS1117-3.3 | U1 | SOT-223-3_TabPin2 | C6186 | 1
8MHz 10ppm (X50328MSB2GI) | X1 | Crystal_SMD_5032-2Pin_5.0x3.2mm | C115962 | 1
NTC 10k | NTC1 | R_0603_1608Metric | C76589 | 1
USB Micro U-D-M5DD-W-1 | USB1 | USB_Micro-B_Wuerth_614105150721_Vertical | C145795 | 1
Conn_01x02 | J1 | JST_PH_B2B-PH-K_1x02_P2.00mm_Vertical | C131337 | 1
On/Off | J4 | JST_PH_B2B-PH-K_1x02_P2.00mm_Vertical | C131337 | 1
Conn_01x03 | J3 | JST_PH_B3B-PH-K_1x03_P2.00mm_Vertical | C131339 | 1
Conn_01x07 | J2 | JST_PH_B7B-PH-K_1x07_P2.00mm_Vertical | C157981 | 1
UNUSED MCU PINS | J5 | PinHeader_2x05_P2.00mm_Vertical | C225290 | 1
HALL/Encoder | P4 | PH-6AK | C146086 | 1
SWD | P5 | PinHeader_1x05_P2.54mm_Vertical | C225480 | 1
NCEP60T20 | Q1, Q2, Q3, Q4, Q5, Q6 | TO-220-3_Horizontal_TabUp_no_hole | C284868 | 6

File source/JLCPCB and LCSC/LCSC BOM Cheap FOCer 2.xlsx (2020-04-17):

LCSC Part Number | Manufacture Part Number | Manufacturer | Customer NO. | Package | Description | RoHS | Order Qty. | Min\Mult Order Qty. | Unit Price | Order Price
C153035 | FS55X106K101EHG | PSA(Prosperity Dielectrics) |  | 2220 | Multilayer Ceramic Capacitors MLCC - SMD/SMT 10uF 100V 2220 RoHS | Yes | 3 | 1\1 | $0.516667 | $3.1
C266430 | SMNR6028-220MT | SXN(Shun Xiang Nuo Elec) |  | SMD,6x6x3mm | Inductors (SMD) SMD,6x6x3mm RoHS | Yes | 5 | 5\5 | $0.09423 | $0.47
C385986 | HMK325C7475KMHPE | Taiyo Yuden |  | 1210 | Multilayer Ceramic Capacitors MLCC - SMD/SMT 4.7uF 100V 1210 RoHS | Yes | 2 | 1\1 | $0.251515 | $1.01
C396088 | SE60210GA | SINO-IC |  | TO-220 | MOSFET N Channel 60V 210A 4V @ 250uA 2.6mΩ @ 20A,10V TO-220 RoHS | Yes | 6 | 1\1 | $0.443939 | $5.33
C437643 | 63ZLJ330M10X20 | Rubycon |  | Radial,10x20mm | Aluminum Electrolytic Capacitors - Leaded 330uF ±20% 63V Radial,10x20mm RoHS | Yes | 2 | 1\1 | $0.284848 | $1.14
C131339 | B3B-PH-K-S(LF)(SN) | JST Sales America |  | Through Hole | PH Header Male Pin 0.079"(2.00mm) 3 Through Hole Wire To Board / Wire To Wire Connector RoHS | yes | 10 | 10 | 0.033033 | 0.33
C131337 | B2B-PH-K-S(LF)(SN) | JST Sales America |  | Through Hole | PH Header Male Pin 0.079"(2.00mm) 2 Through Hole Wire To Board / Wire To Wire Connector RoHS | yes | 20 | 20 | 0.028961 | 0.58
C131342 | B6B-PH-K-S(LF)(SN) | JST Sales America |  | Through Hole | PH Header Male Pin 0.079"(2.00mm) 6 Through Hole Wire To Board / Wire To Wire Connector RoHS | yes | 10 | 10 | 0.0555 | 0.56
C157981 | B7B-PH-K-S(LF)(SN) | JST Sales America |  | Through Hole,P=2mm | PH Header Male Pin 0.079"(2.00mm) 7 Through Hole,P=2mm Wire To Board / Wire To Wire Connector RoHS | yes | 5 | 5 | 0.075024 | 0.38

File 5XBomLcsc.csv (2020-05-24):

Quantity | Manufacture Part Number | Note
15 | FS55X106K101EHG
5 | SMNR6028-220MT
10 | HMK325C7475KMHPE
30 | NCEP60T18
10 | 63ZLJ330M10X20
5 | B3B-PH-K-S(LF)(SN)
10 | B2B-PH-K-S(LF)(SN)
5 | PH-6AK
5 | B7B-PH-K-S(LF)(SN)
5 | U-D-M5DD-W-1
5 | BMI160 | Optional. Only add this if you have a reflow station
5 | A2541WV-5P
5 | A2005WV-2x5P | Only used for gpio

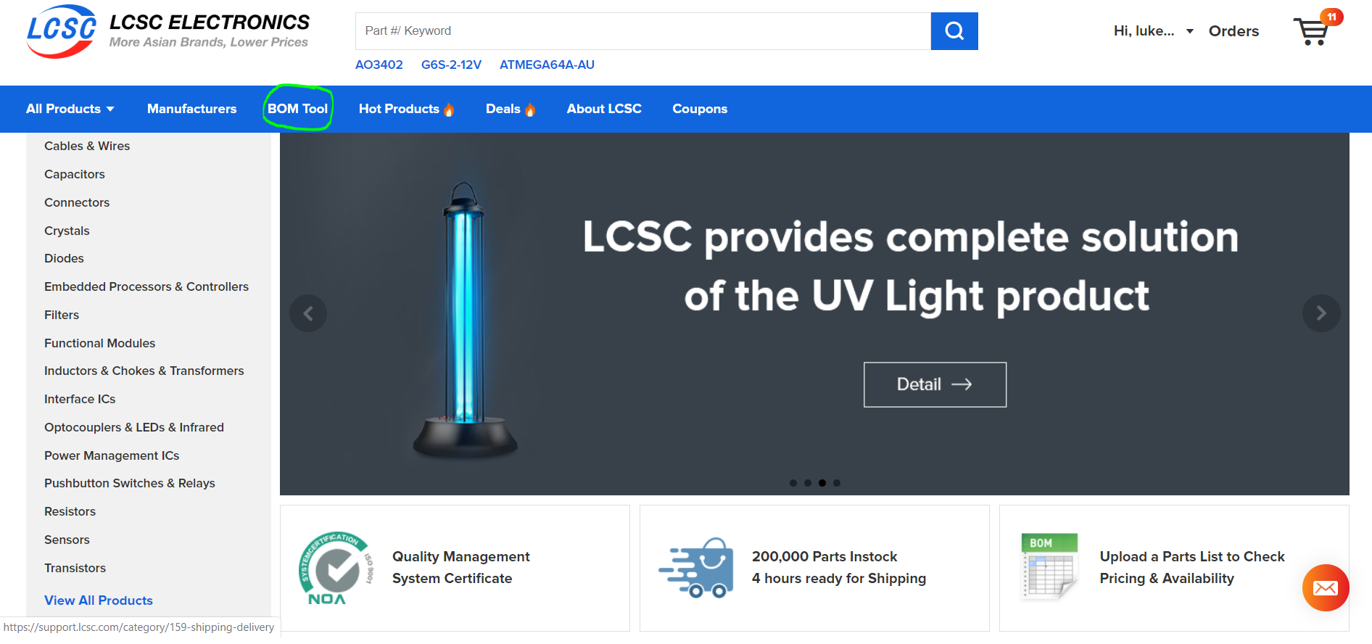
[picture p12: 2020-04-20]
guides/ordering/images/a33759f1b319649d610ba648f7687170_html_dd67901f.png

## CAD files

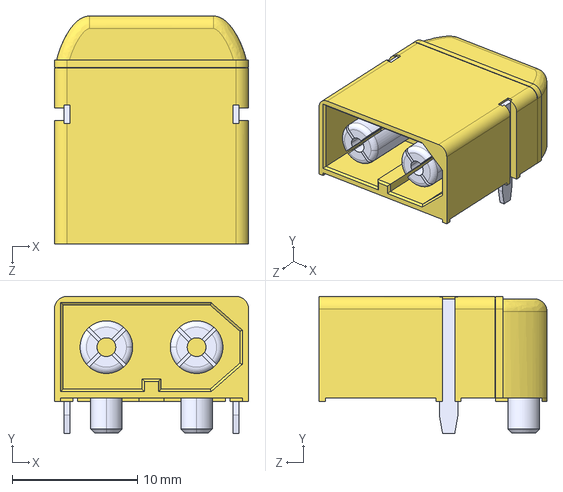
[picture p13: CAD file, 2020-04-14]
source/3D/shapes3D/XT60PW-M --3DModel-STEP-1.STEP
15.5 x 10.9 x 18.2 mm

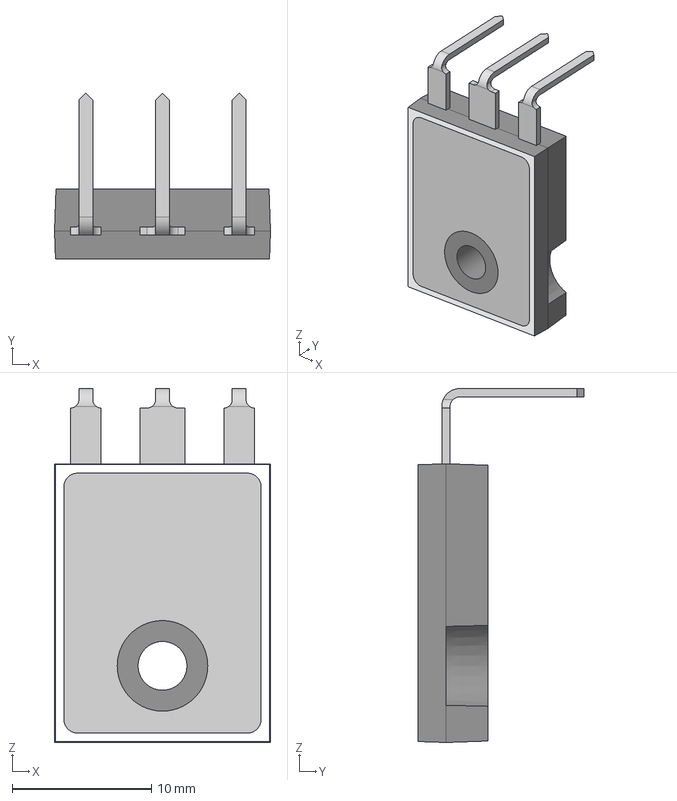
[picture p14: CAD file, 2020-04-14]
source/3D/TO-247H.step
15.5 x 11.9 x 25.4 mm

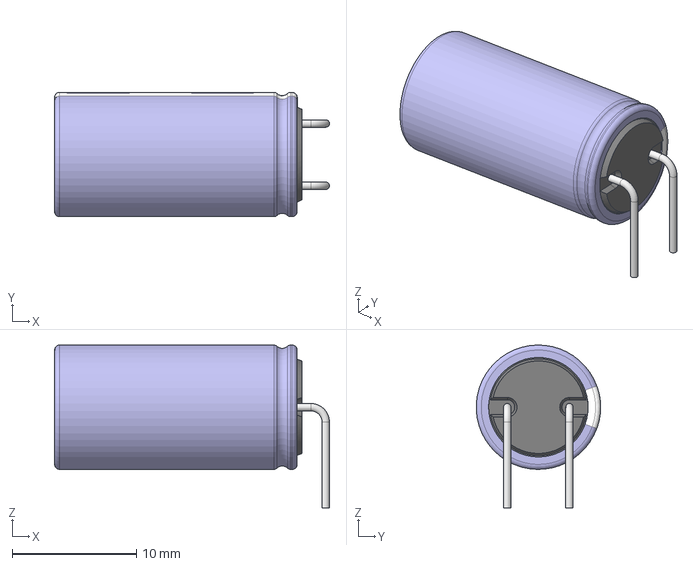
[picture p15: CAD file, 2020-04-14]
source/3D/cap_el_horizontal_d10_h20_pitch5_w0.6.stp
22.1 x 10.0 x 13.1 mm

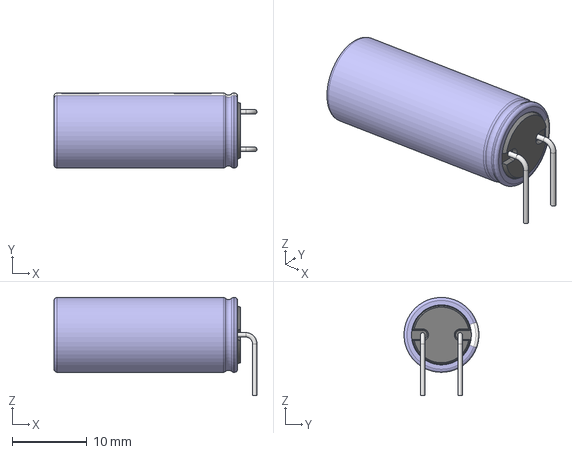
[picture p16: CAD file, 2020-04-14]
source/3D/cap_el_horizontal_d10_h20_pitch5_w0.step
27.1 x 10.0 x 13.1 mm

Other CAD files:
source/3D/cap_el_horizontal_d10_h25_pitch5_w0.step
source/3D/TO-247H.SLDPRT

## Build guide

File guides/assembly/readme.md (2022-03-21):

# Assembly Guide

The following guide explains correct procedures on how to assemble the Cheap FOCer 2(CFOC2).  This includes mounting a flat heat sink. Please **pay close attention** to the details in this guide or else risk damaging the controller during assembly or later during operation. **This is not time for "TLDR"**.

## Prerequisites

* Follow the [Ordering Guide](../ordering) and receive mostly SMD assembled PCB
* Obtain all required [Parts](partsList.md)
* Learn how to solder tiny things [reading style](https://www.overclockers.com/how-to-solder-tiny-things/)
or [video style](https://youtu.be/b9FC9fAlfQE)

## What your board should look like

Take a look at the front and back of the SMD assembled images below:
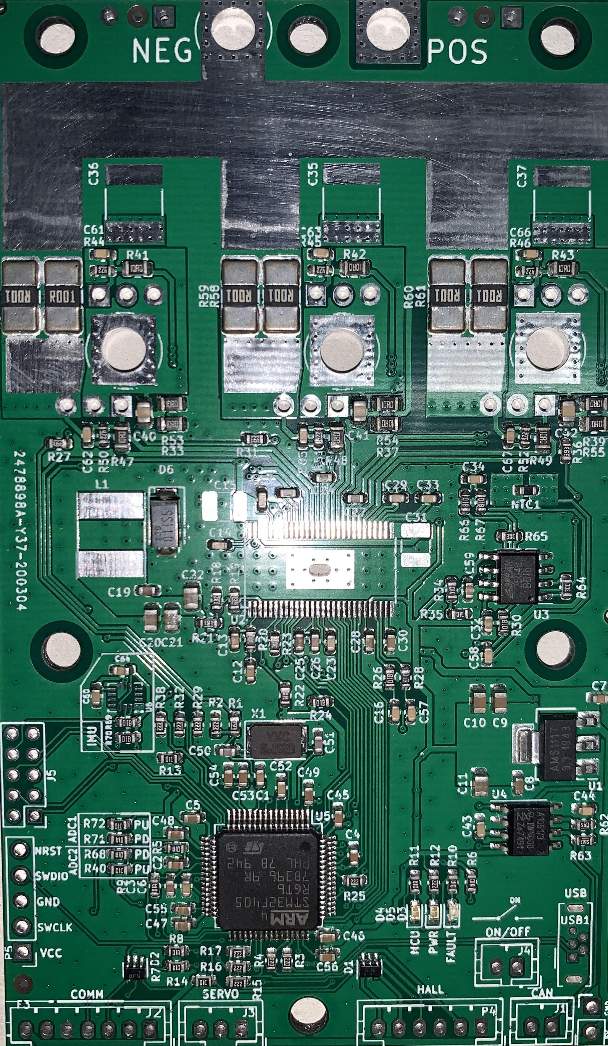
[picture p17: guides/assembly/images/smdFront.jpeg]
front
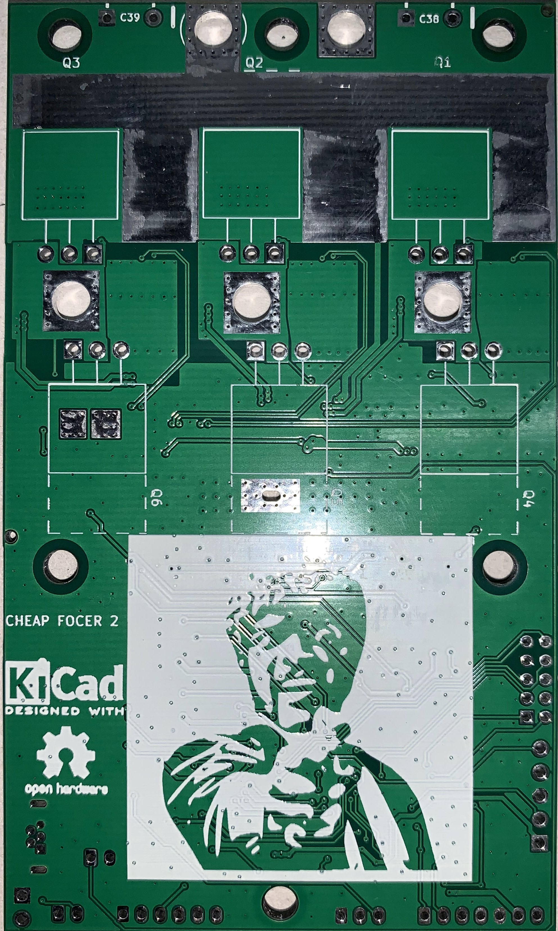
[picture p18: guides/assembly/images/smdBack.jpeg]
back
 
 This is what your PCB should look like(minus the adc1 and 2 resistors) after the CFOC2 is mostly SMD assembled by JLCPCB.  Note the DRV8301 is absent on the board due to lack of stock. It is recommended that JLCPCB provide and assemble the DRV8301 when possible.  Otherwise, you will have to do something like [this](https://youtu.be/k5N07ByY6Hc?t=399) to put it on.

## Tapping Heat Sink

1. Grab your [heat sink and CFOC2 PCB](images/heatSinkAndPCB.jpeg)

1. Temporarily fasten PCB to heat sink like this:
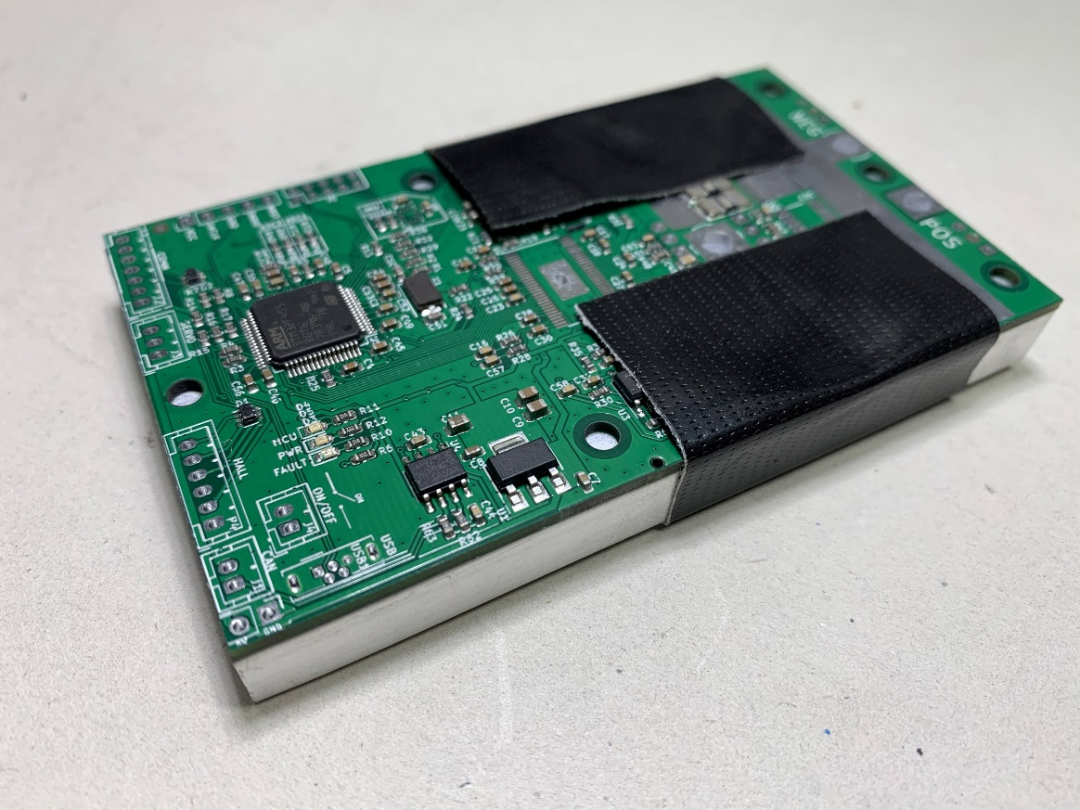
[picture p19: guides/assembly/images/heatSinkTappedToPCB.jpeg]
    

1. Mark the center of the 6 mounting holes on the heat sink with a marker or a hammer and something sharp like a nail to [make a center hole punch](https://www.youtube.com/watch?v=r5vngxToqi4)
1. [Drill and tap](https://www.youtube.com/watch?v=LuqliWT1k5A) the 6 mounting holes for M3 screws. Drill the holes with a 2.5mm drill bit and then tap the threads. If you do not have a tap, you can *carefully* tap the threads by forcing one of the steel M3 screws through the softer aluminum holes then backing out when there is resistance. Clean the screw/tap after backing out.  Turn the screw/tap slowly and use some oil to help. If done too carelessly, the M3 screw/tap could break off in the hole.  If you have a grinder you can also try [this](https://www.youtube.com/watch?v=7Ewu6VOrgU8)

## MOSFETs

1. Bend all MOSFET legs at a 90-degree angle as shown in the figure below. Bend at the location just before the legs widen. Ideally a tool is used secure the body of the MOSFET and also to bend all the legs at once as per the guidance given in the "Lead Bending" section of [this document](http://www.aosmd.com/res/application_notes/package/AN101_TO220_Guidelines.pdf).
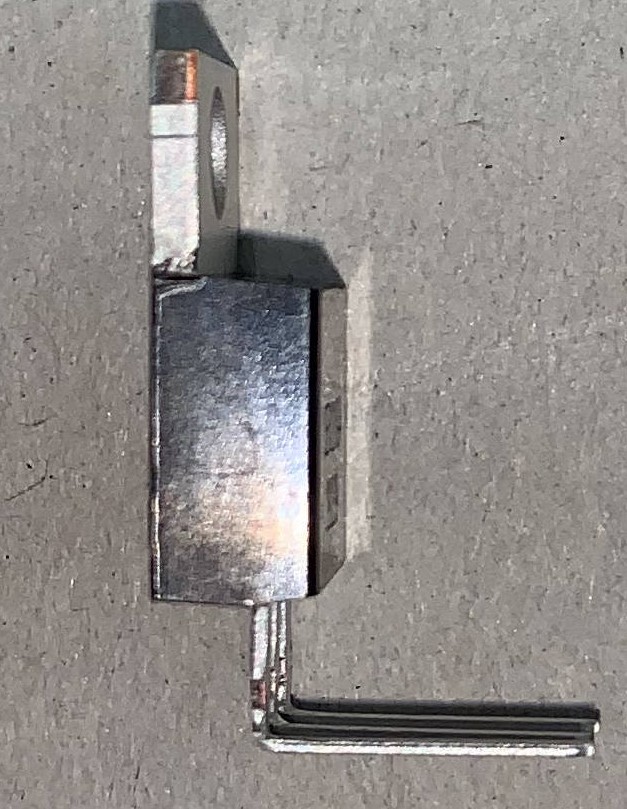
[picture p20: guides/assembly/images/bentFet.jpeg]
    

1. Locate the exposed pads on the backside of the PCB and apply a small amount of **thermal paste**. This ensures good thermal coupling of the NTC resistor that is responsible for measuring the temperature of the MOSFETs during operation.
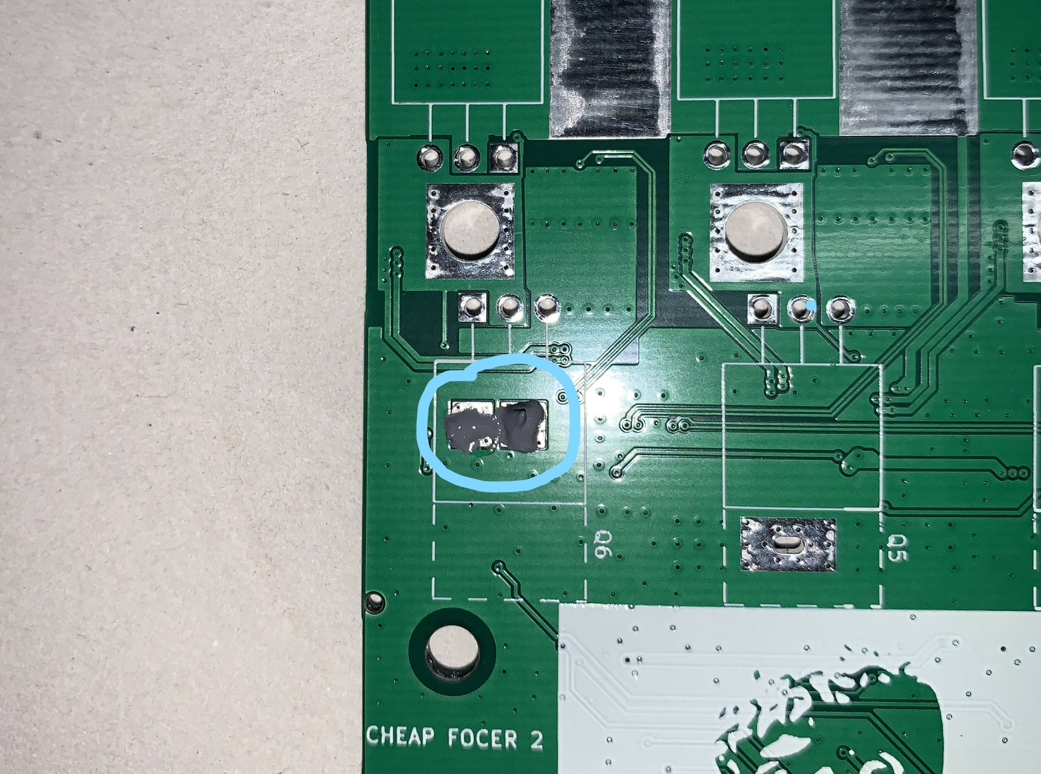
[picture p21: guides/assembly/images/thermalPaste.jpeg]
    

1. Place all MOSFETs in the location and orientation as shown below:
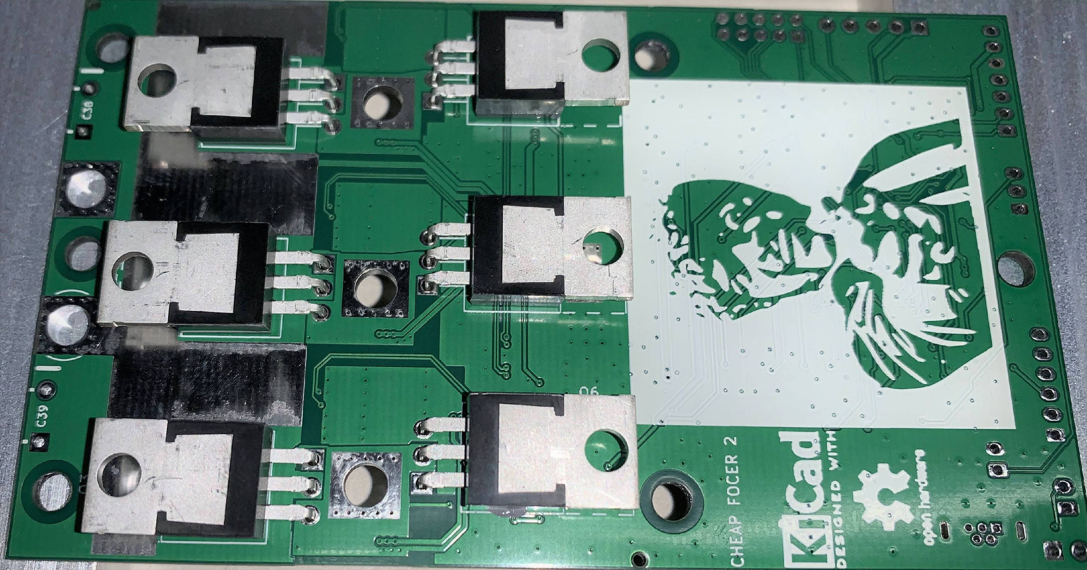
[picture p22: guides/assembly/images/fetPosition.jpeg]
    

1. Make sure the MOSFETs are placed flat against the board like this:
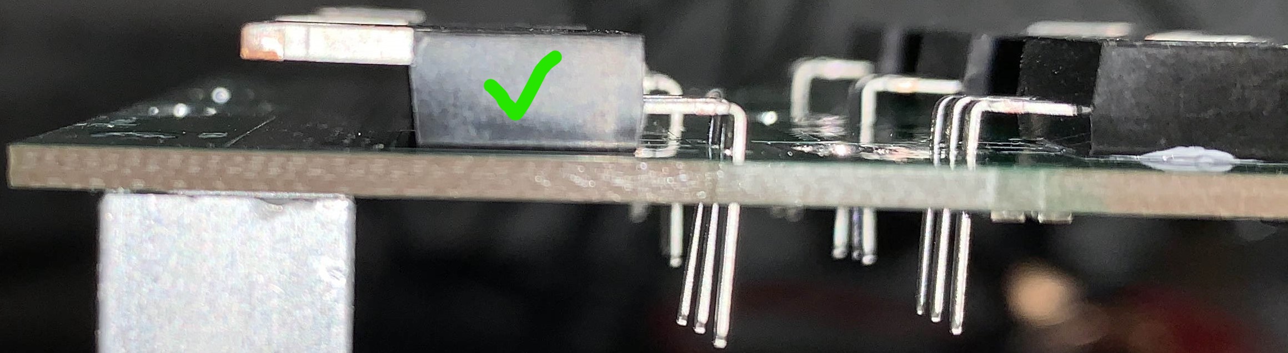
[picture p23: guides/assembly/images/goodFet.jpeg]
    
    Not this:
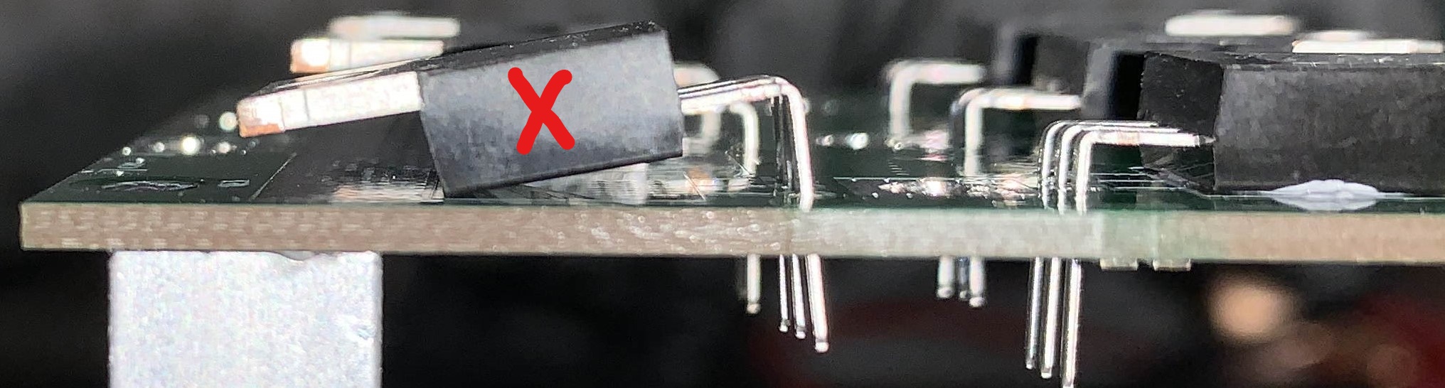
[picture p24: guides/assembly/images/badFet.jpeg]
    

    It is imperative that all MOSFETs be placed and held flush to the PCB surface. Failure to do so will cause a misalignment with the heat sink surface and cause damage to the PCB.

1. While holding down the MOSFET, solder the MOSFET legs that go through the square pad as shown below.  This will tack down the MOSFET into place during the next steps. Do not solder all of the legs yet.  It is advised to apply pressure to the MOSFET in order to ensure it stays flush to the PCB during soldering. Double check all MOSFETs after soldering to verify that the MOSFET bodies are flush to the PCB.
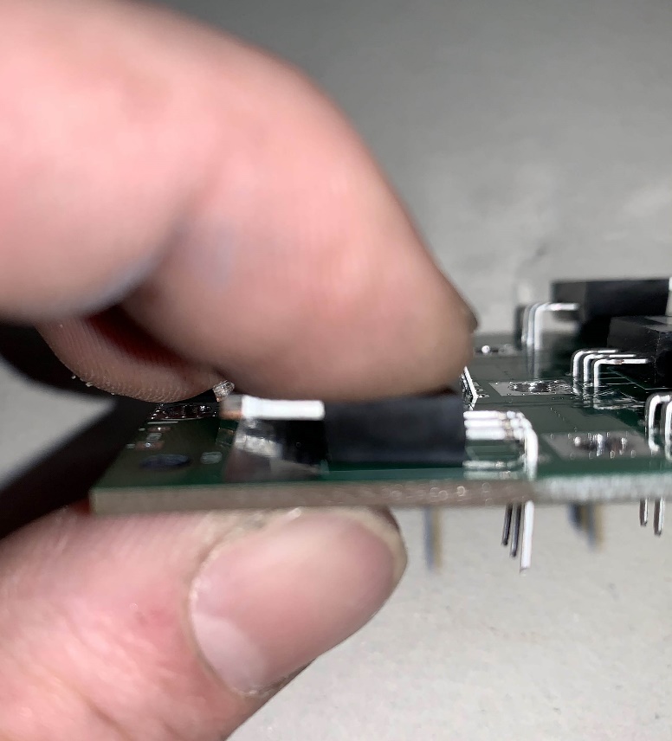
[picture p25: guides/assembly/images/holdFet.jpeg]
    
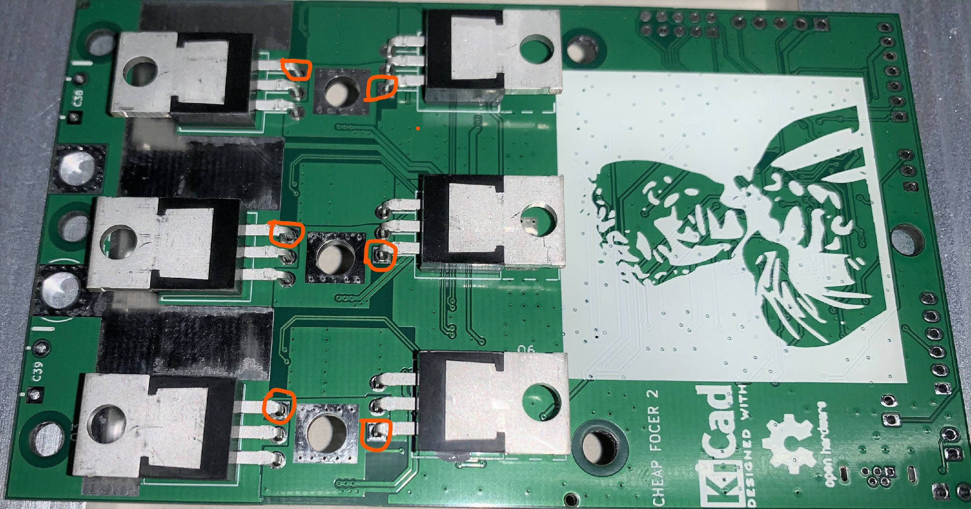
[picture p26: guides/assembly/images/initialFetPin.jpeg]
    

1. Flip PCB over and bend the relevant MOSFET legs into their positions as shown below. Note that not all legs get bent. Bending the legs like this will add copper to the high-current portions of the PCB which helps handle the current.
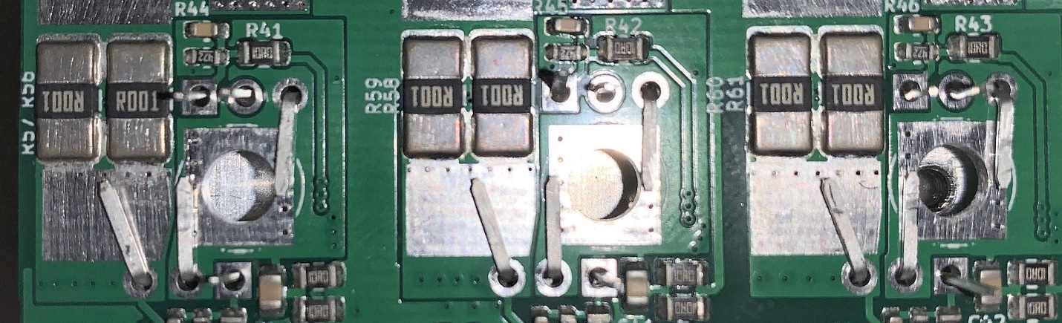
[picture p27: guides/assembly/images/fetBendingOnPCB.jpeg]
    

1. Solder all legs to their respective locations and pads on the top of the PCB. Add excess solder to the leg bent toward the larger current sense resistors(shown in the picture below in yellow). This adds conductive material and thermal mass to help handle the high current.

    Do not add excess solder to the legs close to the large circular hole(shown in the picture below in pink). This hole will be where the motor phase cable will be soldered later. Trim excess leg material from legs that were not bent.

    Make sure that no solder bridges exist between legs(shown in the picture below in pink).
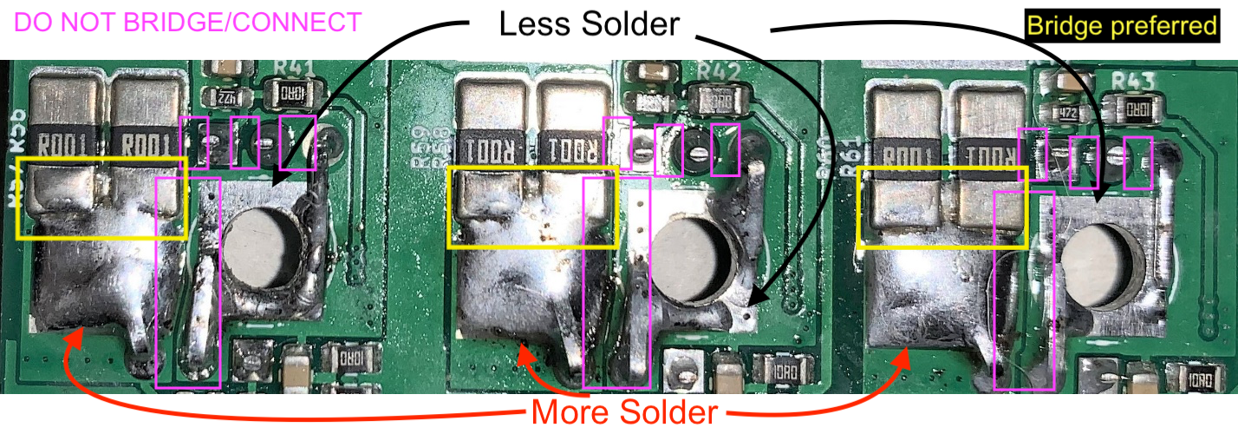
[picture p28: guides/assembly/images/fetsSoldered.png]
    

1. Flip PCB over and solder MOSFET legs from the bottom side. Soldering from both top and bottom ensures both good conductivity and mechanical security.

    It is advised to apply excess solder to the thinner portions of the legs up to the point to where the legs widen. This adds more conductive material to the MOSFET legs where it is needed. Be sure to not create solder bridges between MOSFET legs.
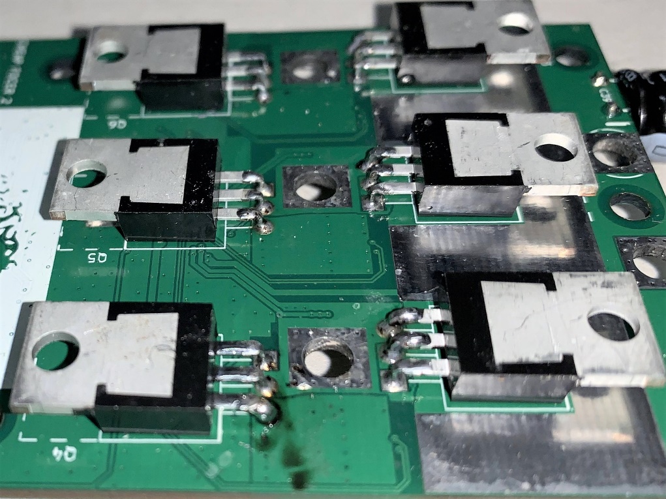
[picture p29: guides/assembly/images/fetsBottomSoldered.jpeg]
    

## Solder All Remaining Components, Wires and Connectors

All [diodes](images/diodPol.png) should be taken care of by JLCPCB. The only other polarized components are the [electrolytic caps](images/capPol.jpg). The square PCB marking is positive and the circle is for negative as shown below:
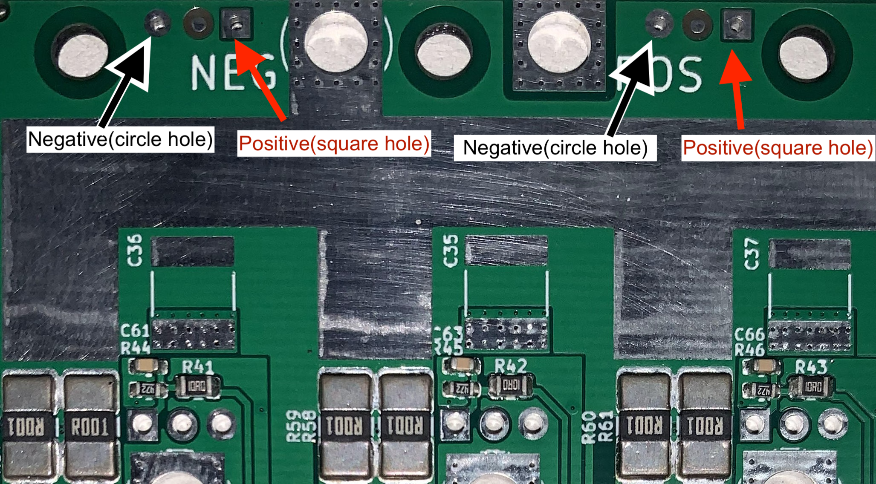
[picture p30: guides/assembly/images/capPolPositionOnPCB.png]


If JLCPCB was out of stock for a polarized component please see the silkscreen marking on the PCB in white showing correct orientation for each polarized components.  Examples include:

* Semi-complete white rectangle silkscreen marking around diode. The absent side of the rectangle marks the Cathode(negative). The other side is the Anode(positive) as shown below:

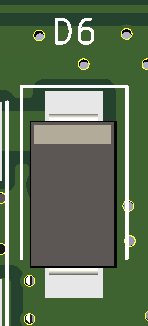
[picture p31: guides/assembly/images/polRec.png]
    

* Same for LEDs since they too are diodes.

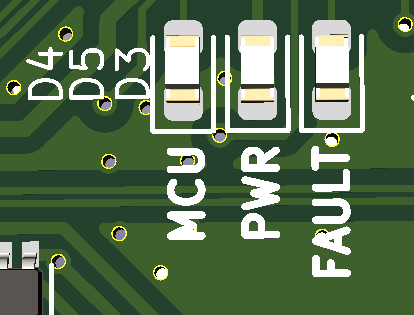
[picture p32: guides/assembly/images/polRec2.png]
    

* Electrolytic caps can vary in how they’re marked but this one has a white line by the negative terminal:
  
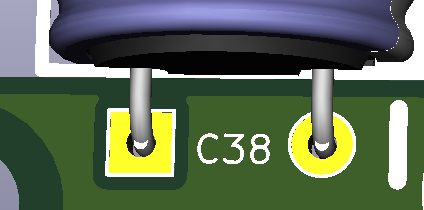
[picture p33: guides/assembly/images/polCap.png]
    

If you have any other questions regarding part placement and polarity please see the fully assembled image below.  If all else fails open the `Cheap FOCer 2 60mm.pro` file in the `source` folder with [KiCAD](https://www.kicad-pcb.org/) as shown [here](images/kiCad.gif).
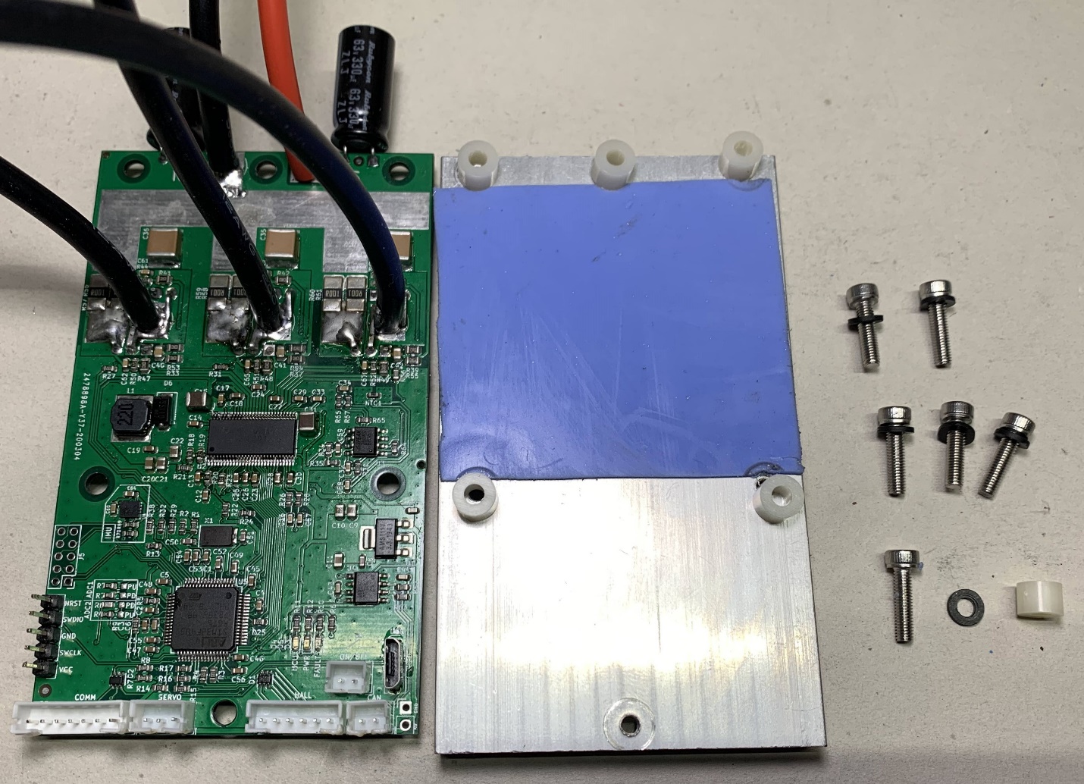
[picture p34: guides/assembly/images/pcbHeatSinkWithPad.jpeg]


If you still have questions feel free to open a [github issue](https://github.com/shamansystems/Cheap-FOCer-2/issues).

## Mounting the Heat Sink

1. Trim excess motor and DC power cable ends on the bottom of the PCB so that there is not risk of the cables being shorting to the heat sink.  

1. Cut your thermal pad to 60mm x 51mm

1. Assemble the fastening hardware, PCB, thermal pad and heat sink as shown in the image below.

    Make sure the thermal pad isn't being pinched between the nylon spacers in the heat sink. This will cause a misalignment in spacing which could cause excess stress to the PCB.

    Apply a small dab of thread lock to the bottoms of each screw.  Carefully tighten screws in the same manor as tightening lug nuts on a tire. Start with the middle screws on the top and bottom. Tighten until just barely snug and then do the same to the other screws. Do not fully tighten until all screws have had some amount of tightening and there is a relatively even amount of pressure on the PCB from all mounting points. There should be no air gaps between the nylon spacers, pcb or heat sink.  Also check to make sure there are no air gaps between the MOSFET tabs and the thermal pad as shown below:
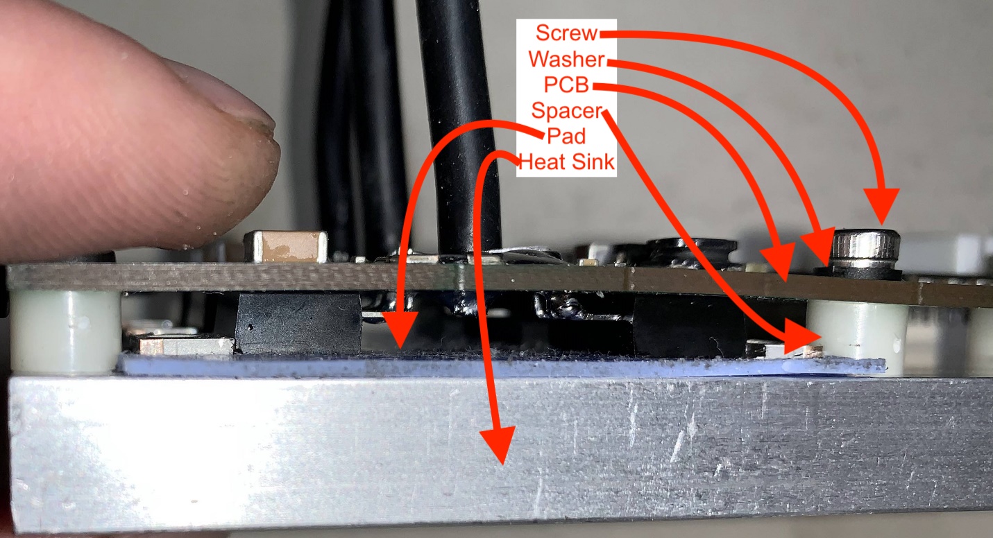
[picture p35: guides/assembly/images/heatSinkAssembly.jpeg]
    

## Power on and Cross Your Fingers

It is now time to power on the controller to conduct a quick test. It is preferable to conduct this initial power up with a current-limited power supply set to 100mA or a cheap 100mA power adapter.  When powered on, the controller should only draw as much roughly 70mA. If a current-limited power supply or 100mA power adapter is not available, then powering up through an anti-spark connector is second best. The blue LED should illuminate if power is successfully flowing through the controller.

## Celebrate and Flash the VESC Bootloader

The controller is now ready to be programed. Please follow [this guide](../flashing/flashing.md) to install the bootloader and CFOC2 [firmware](../../firmware/latest) located in the firmware folder of the repository files.  Use these pins for flashing the bootloader with the st-link:
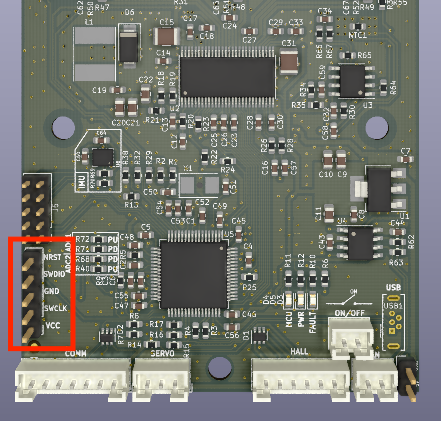
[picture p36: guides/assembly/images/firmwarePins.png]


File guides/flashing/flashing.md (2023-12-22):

# Flashing

## Parts

* st-link
* [Pin Headers](../assembly/partsList.md#pin-headers-aliexpresshttpswwwaliexpresscomitem4000909558952html)

## Instructions

* Works on Mac, Windows and Linux
* Get [STM32CubeProgrammer](https://www.st.com/content/my_st_com/en/products/development-tools/software-development-tools/stm32-software-development-tools/stm32-programmers/stm32cubeprog.licens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)
* Install it
  * **Mac** users need to extract the zip file then right click the `SetupSTM32CubeProgrammer-2.10.0.app` file and click `Show Package Contents` as shown below:
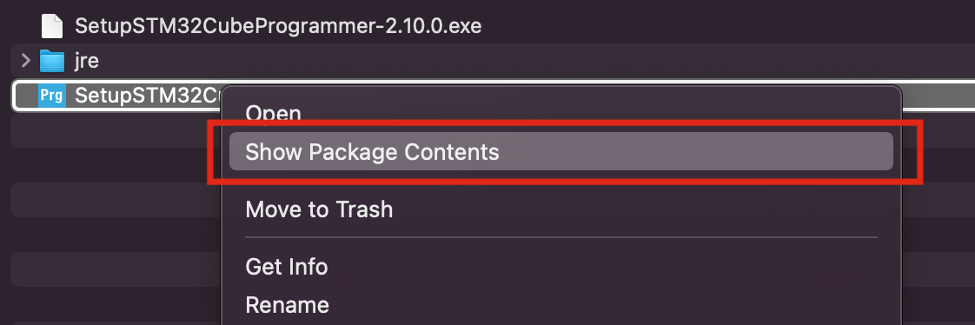
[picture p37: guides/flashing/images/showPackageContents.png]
showPackageContents
    * 
  * Next, open the `Contents` folder
  * Next, open the `MacOs` folder
  * Finally, open the `SetupSTM32CubeProgrammer-2_10_0_macos` file to run the setup
* Open the app
* Plug your USB programmer into your focer
  * VCC=3.3v
  * The other names of the pins match the programmer's pin names
  * No need to plug focer into your big battery just USB power is coo
* Plug your USB programmer into your computer
* Click `connect`:
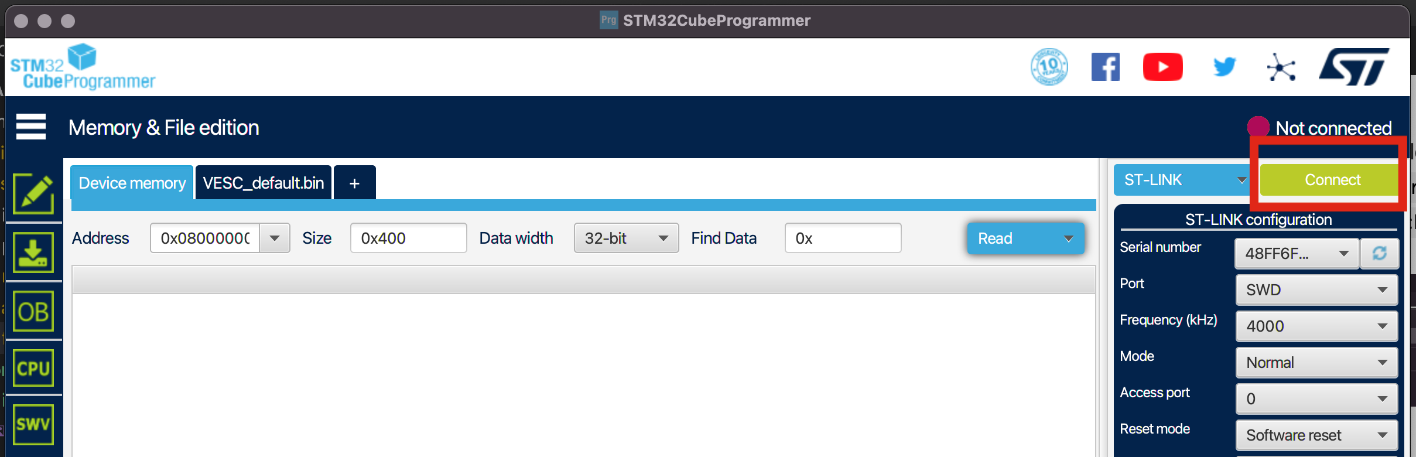
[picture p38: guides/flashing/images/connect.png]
connect
  * 
* Click `read`:
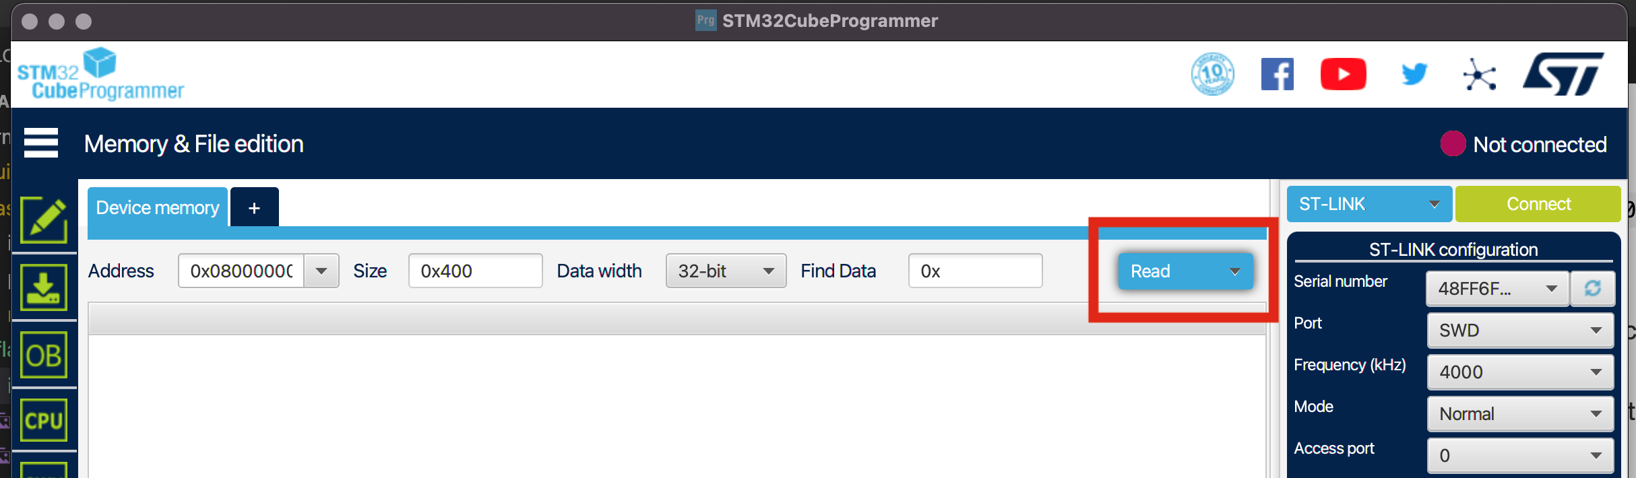
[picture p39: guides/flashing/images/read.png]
read
  * 
* Click `+`:
* Click 'Open file':
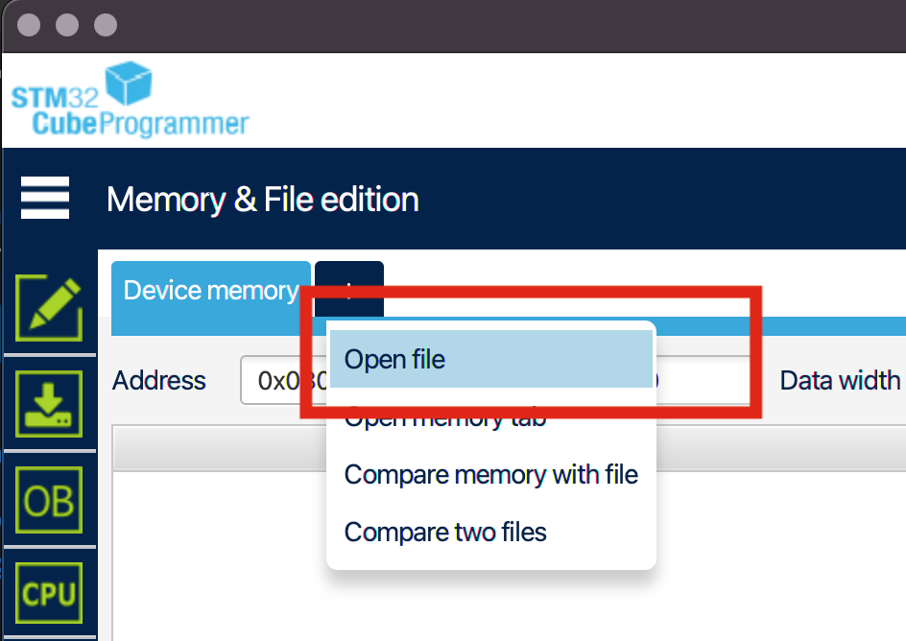
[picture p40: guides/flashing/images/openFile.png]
openFile
  * 
* Select [this](./../../firmware/latest/BLDC_4_ChibiOS.bin) file
* Click `Download`:
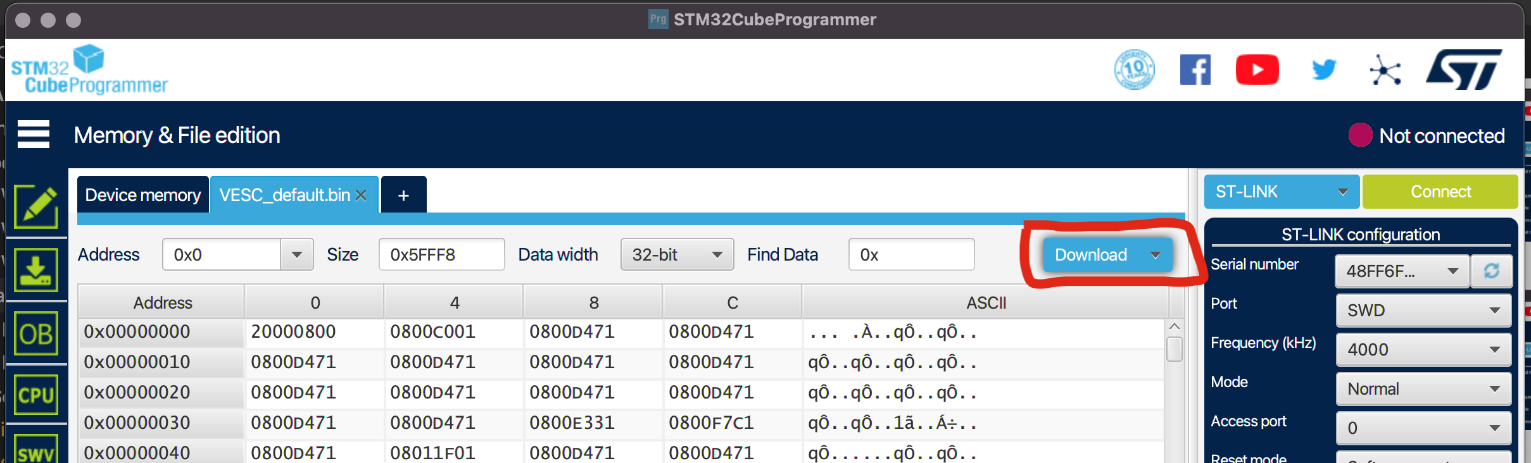
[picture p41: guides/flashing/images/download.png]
download
  * 
* Click `verify`:
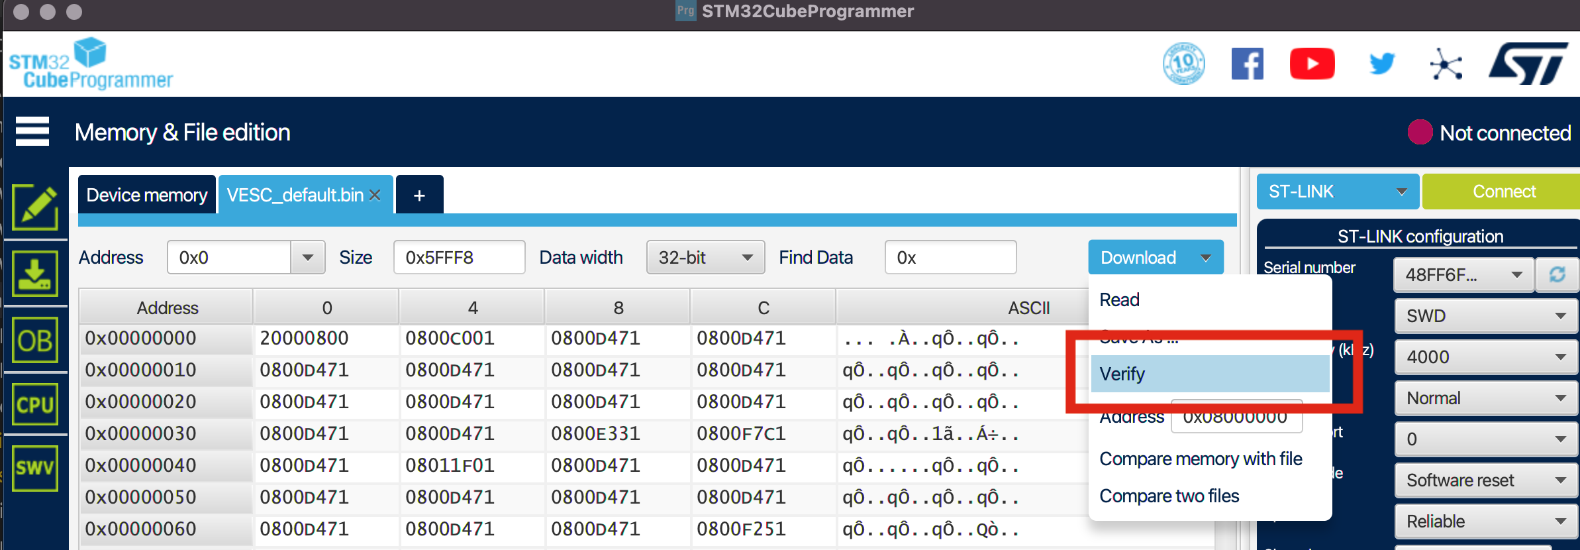
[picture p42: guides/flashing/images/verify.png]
verify
  * 
* Verify that there are no errors
* If there are no errors
		* Click the disconnect button
		* Unplug the st-link
		* Reboot the controller
* Done 🎉

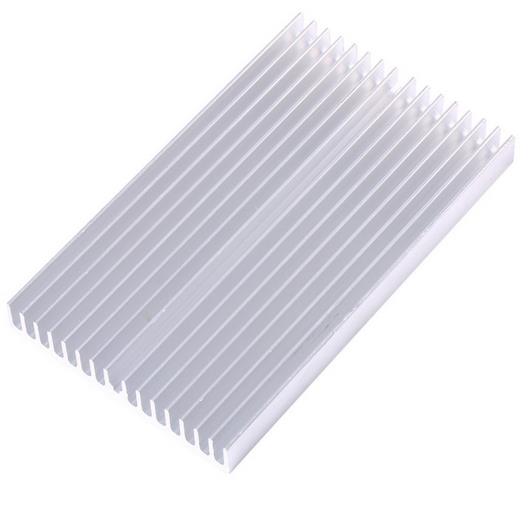
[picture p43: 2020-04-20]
guides/assembly/images/heatSink.jpeg

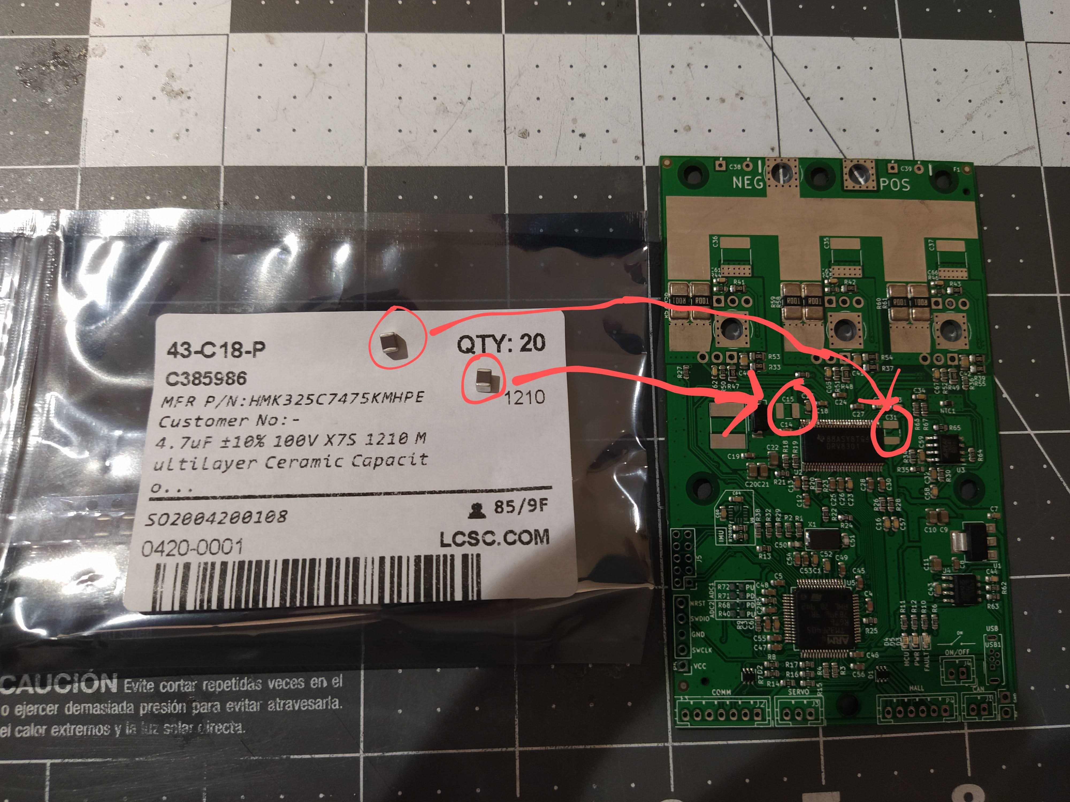
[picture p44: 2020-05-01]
guides/assembly/images/CFOC2_placement_c15_c31.jpg

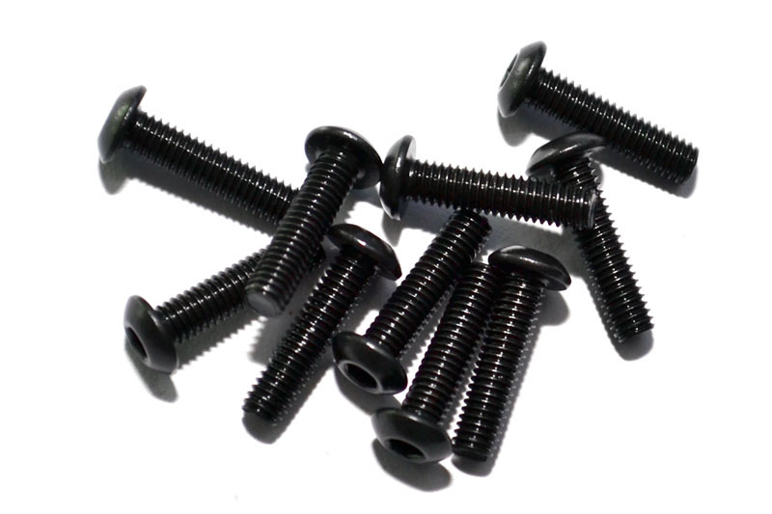
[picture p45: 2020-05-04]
guides/assembly/images/screws.jpg

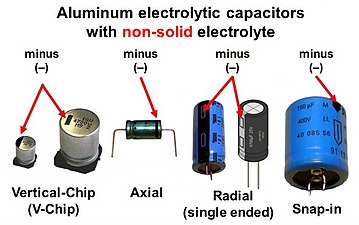
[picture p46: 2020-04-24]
guides/assembly/images/capPol.jpg

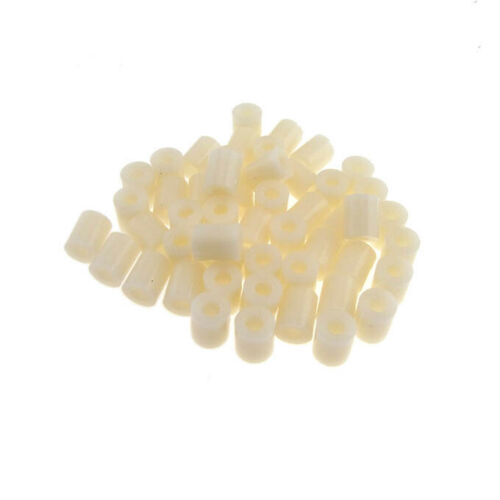
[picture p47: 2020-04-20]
guides/assembly/images/spacers.jpeg

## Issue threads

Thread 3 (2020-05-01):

B6B-PH-K-S(LF)(SN) Discontinued

Helno, 2020-05-01:
Discontinued.

https://lcsc.com/product-detail/Wire-To-Board-Wire-To-Wire-Connector_JST-Sales-America_B6B-PH-K-S-LF-SN_JST-Sales-America-B6B-PH-K-S-LF-SN_C160289.html

This appears to be a compatible replacement.

https://lcsc.com/product-detail/Wire-To-Board-Wire-To-Wire-Connector_JST-Sales-America-B6B-PH-K-LF-SN_C274409.html

bj97301, 2020-05-10:
Good find.  @shamansystems if it looks good to you I will replace it in the Lcsc bom file.

shamansystems, 2020-05-12:
https://lcsc.com/product-detail/Wire-To-Board-Wire-To-Wire-Connector_BOOMELE-Boom-Precision-Elec-PH-7A_C10398.html

https://lcsc.com/product-detail/Wire-To-Board-Wire-To-Wire-Connector_CJT-Changjiang-Connectors-A2001WV-7P_C225193.html

These look compatible as well. Price points cater to different quantities though. I'm down with replacing with helno's suggestion, either of mine, or all of them since we have an "alternatives" list going.

Helno, 2020-05-12:
Those two you listed are 7 pin.

I'm sure there is something out there that is cheap and available in multiples of 5.

shamansystems, 2020-05-13:
Ah yes my mistake. I’ll look again

Helno, 2020-05-19:
How about these.

https://lcsc.com/product-detail/Wire-To-Board-Wire-To-Wire-Connector_CJT-Changjiang-Connectors-A2001WV-6P_C225192.html

Minimum order 10 cost for 10 is $0.37

Or these.

https://lcsc.com/product-detail/Wire-To-Board-Wire-To-Wire-Connector_BOOMELE-Boom-Precision-Elec-PH-6AK_C146086.html

Minimum order 20 cost for 20 is $0.35

The boom ones are cheaper but the BOM will need a note for people ordering more than 5 at a time so they don't order 100 of these when they don't need to.

shamansystems, 2020-05-21:
I'm down for the cheapest approach even though it's more connectors than needed. Notes can be added to alert people of the MOQ

Helno, 2020-05-21:
Even with the increased min it lowers the over all cost.

What is the easiest way to update that spreadsheet? I don't see an easy way to do a pull request on it.

Closed 2020-05-24.

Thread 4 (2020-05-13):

U1/AMS1117-3.3 and other zero rotation error in JLCPCB

hackerboygn, 2020-05-13:
check U1 and other  other multi-pin components in https://github.com/shamansystems/Cheap-FOCer-2/blob/master/guides/ordering/images/a33759f1b319649d610ba648f7687170_html_a3977b4e.png, as you see , their direction error.

This footprint Package_TO_SOT_SMD:SOT-223-3_TabPin2 and other in KiCAD library conforms to the IPC standard, but JLCPCB NOT!
JLCPCB stipulates that the positioning hole of the package materials tape and reelis on the left side is zero rotation, more information ref http://club.szlcsc.com/article/details_116_1.html, http://club.szlcsc.com/article/details_1569_1.html and https://www.maximintegrated.com/en/design/packaging/package-information/smd-tape-reel-info.html.

Although reminded everyone in the  ordering guide, but I think should be modified use the JLCPCB standard librarys.

Thanks share this project again!

shamansystems, 2020-05-13:
Hey thanks for your input!

Yes true that JLCPCB doesn’t use KiCADs placement standard (IPC) and I was aware of this. However, JLCPCB does a good job correcting the placement of components in their DFM review. I’d rather not deviate form the IPC standard in case people want to use other vendors. As long as it works the way it is, I’d rather not fix what ain’t broken.

hackerboygn, 2020-05-21:
> Hey thanks for your input!
>
> Yes true that JLCPCB doesn’t use KiCADs placement standard (IPC) and I was aware of this. However, JLCPCB does a good job correcting the placement of components in their DFM review. I’d rather not deviate form the IPC standard in case people want to use other vendors. As long as it works the way it is, I’d rather not fix what ain’t broken.

I think you are right, I have made one too, thanks again！

Closed 2020-05-21.

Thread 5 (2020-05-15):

Schematics in PDF

Peemouse, 2020-05-15:
Hi,

Thanks for this awesome project !
Is it possible to generate and include a PDF version of Schematics in the repo ?
Or did I miss it ?

That would ease the reading without downloading the whole project (and avoid installing Kicad).

Thanks !

Clément

shamansystems, 2020-05-15:
Yes I can and should do this. I’m out of town but I’ll get to it once I return

shamansystems, 2020-05-21:
Done!

Closed 2020-05-21.

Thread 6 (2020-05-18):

bootloader

MegaC-C, 2020-05-18:
since the url for the bootloader in the mentioned tutorial is broken, i thought it might be helpful to share a working bootloader.

https://github.com/vedderb/vesc_tool/blob/master/res/bootloaders/60_o_75_300_o_HD_o_UAVC_OMEGA_o_75_300_R2_o_60_MK3_o_100_250_o_75_300_R3_o_60_MK4_o_60_MK5_o_HD_R2.b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

this bootloader worked fine for me:)

shamansystems, 2020-05-21:
Bootloader is now in the repo

Closed 2020-05-21.

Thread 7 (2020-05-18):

nRF51 using Windows

MegaC-C, 2020-05-18:
The vesc-tool SWD programmer couldn't detect my Waveshare nRF51822 module.
So i used openocd (for Windows) and the ST-Link V2 to flash the nRF51822 chip. I didn't know openocd and still don't undestand it, but here is how it worked for me:

-download & extract the precompiled openocd for Windows from here: https://gnutoolchains.com/arm-eabi/openocd/

-open the bin folder (it should contain two .dll files and the openocd.exe)
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

-download the openocd.cfg file from here: https://github.com/vedderb/nrf51_vesc

-download the correct .bin file for your module from here: https://github.com/vedderb/nrf51_vesc/tree/master/build_all
(my module has 32kB RAM and 16MHz clock, so i chose nrf51_vesc_ble_32k_16m_rx11_tx9_led3.bin)

-add the two files to the bin folder of openocd
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

-connect the nRF51 module (SCLK, SDO, VDD, GND) via the ST-Link v2 as described here: https://github.com/vedderb/nrf51_vesc/blob/master/README.md

-open command prompt (windows + cmd) and type:
**cd C:\ _yourPath_ \openocd-20200503\OpenOCD-20200503-0.10.0\bin**        (now you are in the openocd bin folder)

-then type:
**openocd -f openocd.cfg -c "init" -c "halt" -c "nrf51 mass_erase" -c "program nrf51_vesc_ble_32k_16m_rx11_tx9_led3.bin verify reset exit"**        (if you used another .bin file, then type the name of that .bin file of course)
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

-wait until flashing is finished and connect the vesc RX TX pins to the correct pins of your nRF51 module (pins RX<>p0.09 and TX<>p0.11 in this case)

-power the vesc up and connect BLE via the android app

done

MegaC-C, 2020-05-18:
oh and i soldered a 10uF cap between vcc and gnd of the nRF51 module just as Mr. Vedder suggested, i don't know if it was necessary

shamansystems, 2020-05-19:
So what was the issue and what does it have to do with the CFOC2?

MegaC-C, 2020-05-19:
My issue: the CFOC2 could not act as SWD programmer for the nRF51822 module I have (no device detected).

You are right, it is not specifically an issue of the CFOC2. But maybe other CFOC2 users might run into the same problem and it took me quite some time to find a solution. So I thought it helps when all the info is in one repo.

wrong place? ( sorry i'm new to github)

shamansystems, 2020-05-21:
It's fine. I'll close the issue but the info will be retained on this repo.

Closed 2020-05-21.

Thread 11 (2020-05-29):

Is 50.4V(12s) the hard limit?

juodumas, 2020-05-29:
> Up to 50.4V(12s) safe operating voltage. For 20s version take a look at these FOCers.

Can it handle above 50.4V with 20A peak?
I am using 16S LiFePo4, charging up to 56V.

shamansystems, 2020-05-30:
The hardware is designed to handle 12S with good reliability. Anything beyond with not be as reliable and you risk damaging the FETs or DRV. 16S will almost certainly cause damage.

Closed 2020-05-30.

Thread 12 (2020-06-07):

STEP model is deprecated

MayorBug, 2020-06-07:
Current 3D STEP model doesn't match the latest design revision.

Closed 2020-06-07.

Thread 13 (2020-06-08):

Wrong firmware

charclo, 2020-06-08:
When I upload the firmware with vesc tool through usb I get "Hw: FOCer". The source code also compiles for the Serious focer. I had to adjust "conf_general.h" so I could compile and upload the firmware

charclo, 2020-06-08:
After my uploading over usb problems stopped I can't reproduce this anymore. Now both the firmware from 5.01 folder and latest give me a cheap focer firmware. I don't know where the focer firmware came from before as I hadn't compiled any myself then.

Closed 2020-06-08.

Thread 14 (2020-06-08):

Very slow firmware update over usb (Mac)

charclo, 2020-06-08:
The firmware update is very slow (>10 min) and fails often with a time out warning. I tried 2 different (cheap) usb cables.
I'm running mac os 10.14.6 with the vesc tool I compiled from vedders github repo

charclo, 2020-06-08:
After switching to a precompiled version this is not happening anymore. So this is not a cheap focer issue

Closed 2020-06-08.

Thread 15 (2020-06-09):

conf_general.h refers to hw_FOCer.c while ref to hw_FOCer_2.c commented out

shanghaijo, 2020-06-09:
Line 153: #define HW_SOURCE "hw_FOCer.c"

while line 150 is commented out: //#define HW_SOURCE "hw_Cheap_FOCer_2.c"

https://github.com/shamansystems/Cheap-FOCer-2/blob/67b7fbcc121aee1f70713e3b77ed3238eb31ad52/firmware/Source%20Code/bldc-master%205.01/bldc-master/conf_general.h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

lachlanh, 2020-07-26:
Made the above change and built the firmware. Builds and uploads ok, but any app other than UART, will work initially after flashing the firmware and then cause all 3 leds to flash on subsequent reboots of the controller at a regular interval and I am not able to connect to the controller.
Is the source in the repo correct ?
Is their a fork of the bldc repo that is more up to date ?
(I am trying to build a custom app so prebuilt firmwares are working fine, but I need one I can build, also awesome project, loving the hardware!)

haidongt, 2020-09-05:
I ran into the same issue. I'm also developing a custom app and the issue is only observed when the firmware is built from source. After some debugging I found that the issue is only present when rebooting after a mcconf or appconf save. If I don't write to flash at all and reboot the board works perfectly fine. I think it must be something with the flash memory but I haven't figured out.

lachlanh, 2020-09-05:
Yup that is the same that I have observed, any change to settings and it fails on the reboot. Have worked around it by building from source with my appconf and mcconf headers compiled in, solves the problem for the present. Writing flash does seem to be a likely cause, was wondering if it was something to do with how I flashed the firmware and the bootloader initially but haven't made any progress figuring it out. If you do figure it out, please post again.

nhedlun1, 2021-01-20:
Hello, im facing the same issue. Did you ever find the source of why this happend? I also tried to just upload the Bootloader but it fails to boot then also. Could there be something with the bootloader? The pre-built firmware in the "latest" folder works as expected though.

nhedlun1, 2021-01-21:
Ok i think this is a compiler issue. I solved the problem by installing GNU Arm Embedded Toolchain: 7-2018-q2-update June 27, 2018, the newest version of arm-none.eabi-gcc does not work. After a APP setting is changed it goes into a boot loop.
I followed these steps, hopefully someone else is helped by this.

Issue on Vedders github describing almost same behaviour: https://github.com/vedderb/bldc/issues/210

How to install specific toolchain: https://freeelectron.ro/arm-cross-compiler-tutorial-stm32/

Link to toolchain i used: https://developer.arm.com/tools-and-software/open-source-software/developer-tools/gnu-toolchain/gnu-rm/downloads/7-2018-q2-update

After i installed the toolchain as per the instructions, i had to run "source ~/.bashrc" or restart terminal to update file.

Hope it helps someone!

haidongt, 2021-01-24:
That also solved my issue. Thanks a lot, nhedlun1!

lachlanh, 2021-03-02:
Thanks nhedlun1, that fixed the issue for me also. Seems to need that version of the arm gcc that you mentioned to be able to write to flash (I was using the version from the ubuntu package repos before that).

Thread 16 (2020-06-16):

Link to bootloader is broken

TechnikWeber, 2020-06-16:
Hello,
I am just ready to start but the link given un the example for flashing the bootloader is broken.

(https://electric-skateboard.builders/t/vesc-boot-loader-installation-tutorial/32103?source_topic_id=52813)

I think its a problem from Vedder Forum, but can you maybe upload it here?

shamansystems, 2020-06-16:
get bootloader from the repo here
https://github.com/shamansystems/Cheap-FOCer-2/tree/master/firmware

I'll have to make note in the guide that the bootloader is available in the repo itself.

TechnikWeber, 2020-06-17:
It’s working now! Thanks!

Closed 2020-06-17.

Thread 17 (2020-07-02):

I was told by JLCPCB that they will no longer order more DRV8301 and found some potential problems with DRV8301

victordlee, 2020-07-02:
I tried to put in my order for FOCer-2 and noticed the DRV8301 was out of stock again.  So, I asked JLCPCB when they would get more in stock.  They told me that they do not plan to order more DRV8301 in the near future due to low demand.  In any case, I asked the question through their chat line so if you want to drive up demand, I suggest you pick chat a couple of times to generate more demand for the part.

I also notice this potential problem with DRV8301...

https://e2e.ti.com/support/motor-drivers/f/38/t/668809

DrPii, 2020-07-06:
Hey,
just wanted to comment on this.
Any plans of integrating the new chip mentioned in the post above?

> The DRV8320R is a newer device with improved features and a more thorough test program

thanks and great Job so far :)

shamansystems, 2020-07-06:
@victordlee unfortunately I don’t have control over what JLCPCB has in stock. As of now, It doesn’t seem they have the DRV8320 in stock either. While I know it’s an older device, the DRV8301 is what has been stocked so far and can be handled by their SMT service. The DRV8320 is a QFN package and difficult for typical DIYers to handle and solder.

DrPii, 2020-07-06:
Ah thanks for that.
I didn't even check if they had the 8320 in stock.

Keep up the great work 😁👍

transcendReality, 2020-07-08:
This guide no longer works. They simply don't have the components. Out of the entire bom and cpl I ordered from LCSC, they only delivered the 100v radial capacitors, a momentary switch, and the IMU. Not a single ceramic cap- no USB connector, no connectors period. I don't have the immense level of patience it would take to figure out what I'm missing, and feel like I've blown my money.

This certainly wasn't as easy as just following a guide.

I don't understand why you just didn't offer people kits?

shamansystems, 2020-07-09:
@transcendReality You're more than welcome to bring your issue and it's details to the support thread mentioned in the readme of this repo. I don't offer kits because this project is meant to enable DIYers and for others to create kits if they want. There's already someone making kits for Europe.

Closed 2020-07-09.

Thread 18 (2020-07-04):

Net C17-Pad2 Connections

SRFirefox, 2020-07-04:
Of the three vias on the C17-Pad2 net clearly intended to connect the bottom side trace to the topside trace under D6, only one via is electrically connected.

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

shamansystems, 2020-07-06:
Good catch! I’ll fix this for the v1.0 release.

shamansystems, 2020-07-09:
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

Fixed!

SRFirefox, 2020-07-13:
Good work!

Closed 2020-07-09.

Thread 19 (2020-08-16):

Ordering instructions differ from board-front pic shown in assembly guide

powneill, 2020-08-16:
Assembly instructions "What your board should look like" section.  Picture shows ADC2/ADC1 section populated with resistors R72, R71, R68, and R40.  However, the BOM and CPL CSV's do not contain any reference to these components for ordering or pick-and-place.

Can you clarify whether this was an omission from CPL/BOM and these components should be added, or whether it is no longer necessary to populate those sections and the assembly guide picture is just outdated?

Thanks much

bj97301, 2020-08-16:
Good catch. These are optional.

Closed 2020-08-16.

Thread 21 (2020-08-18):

2 motors

vfear, 2020-08-18:
Hi, is it possible to connect to two motors from a gyro scooter? or maybe there is a scheme with a double output?

shamansystems, 2020-08-18:
You would have to use 2 CFOC2 controllers that are connected via the CAN bus. Each controller would be controlling 1 motor but would work together.

Dual motor motor operation is a common application for VESC based controllers. You can find a lot of examples and support for this on the esk8 forums

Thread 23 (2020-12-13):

BMI160 Out of Stock at https://lcsc.com/

unRARed, 2020-12-13:
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

Also, out of stock at Mouser and Digikey. Will update if I find somewhere where it is available.

Thunkar, 2021-01-15:
Following, really bad news for a DIY OneWheel...

Thunkar, 2021-01-15:
The only viable alternative I've found is to order a complete board such as this one:

https://www.amazon.es/HiLetgo-Palstance-Accelerometer-Gyroscope-Acceleration/dp/B082M8PTK7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

...and remove the chip using the reflow station. Digikey shows that availability might be limited at least until June, so I might just do that.

unRARed, 2021-01-15:
I was able to purchase a pack of 5 from an eBay listing... from China. Took
about 2 weeks to arrive. Haven’t built anything up yet though.

On Fri, Jan 15, 2021 at 8:29 AM Gregorio Juliana <notifications@github.com>
wrote:

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
--
Regards,
*Ryan Richardson*
360-441-9585 *cell*

Mitchlol, 2021-01-22:
the lsm6ds3 can be placed in the same spot, it would require custom firmware for now (easy small change), however there is talk to make the firmware auto detect the populated IMU.

Closed 2021-04-28.

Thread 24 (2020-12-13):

63ZLJ330M10X20 Out of Stock at https://lcsc.com/

unRARed, 2020-12-13:
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

~In stock [at Mouser](https://www.mouser.com/ProductDetail/Rubycon/63ZLJ330M10X20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), however.~ Nope, also out of stock at Mouser. =/

NickLD, 2020-12-14:
@unRARed I noticed those same caps were out of stock when I ordered parts for a batch of 5 a few weeks ago.
I used the part finder in LCSC to find a drop-in replacement. I used the [C357629](https://lcsc.com/product-detail/Aluminum-Electrolytic-Capacitors-Leaded_BERYL-Electronic-Tech-RG063M331LO10-20TA-1A1E_C357629.html) which have worked just fine on the boards I've made. Only spec difference is they are rated for 7k vs 10k Hrs, but they should be just fine.

unRARed, 2020-12-15:
Thanks, I'll grab these in the case the backorder is indefinite. =)

nespotts, 2020-12-30:
I also just found that there is the same capacitor in just a different length cylinder available (10x25mm) [63ZLJ330M10X25](https://lcsc.com/product-detail/Aluminum-Electrolytic-Capacitors-Leaded_Rubycon-63ZLJ330M10X25_C694362.html).

unRARed, 2020-12-30:
I ended up going with Nick's option. Just received them yesterday so haven't built anything up yet. @shamansystems should I keep this open?

NickLD, 2020-12-30:
Just created a quick PR to add the two alternative options discussed in this issue to the 'out-of-stock' page.
Meant to do that weeks ago, my bad ;)

unRARed, 2020-12-31:
Awesome!

Closed 2020-12-31.

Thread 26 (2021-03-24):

Faul LED blinks 16 times

Fisatec, 2021-03-24:
Hey,
I don't know what happened. Suddenly the fault LED is blinking 16 times in a row, without any incident.
I can connect via Bluetooth, but I cannot execute Motor configurations for example.

Tried disconnecting all Plugs, but did not attain any success

Kind regards
fisatec

shamansystems, 2021-03-24:
Fisatec can you bring the issue over to the esk8 forum for support?

I'll need a more comprehensive description of the conditions and situation in order to help.

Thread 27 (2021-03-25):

What is the minimal voltage for vesc control pins(gpio, uart ect.)?

astra404, 2021-03-25:
I am planning to use stm32 ( blue pill) to control the esc. It is 3.3v only. Will it work with cheap focer?

charclo, 2021-03-26:
The cheap focer also uses an stm32, so 3,3V is perfect

astra404, 2021-03-26:
Good to hear. As I understand focer is also 5v compatable. But logic output is at 3.3v range. Is that correct?

shamansystems, 2021-03-26:
The CFOC2 is capable of supplying 5V to accessories but all of the logic is 3.3V.

astra404, 2021-03-26:
Tank you for the healp!

Closed 2021-04-01.

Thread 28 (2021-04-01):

Cleaning the finished pcb

astra404, 2021-04-01:
Maby this is a dumb question but can I wash the focer by submerging it in izopropanol?
I.e there are no components that are sensitive to IPA and other solvents like bme280 is...

astra404, 2021-04-01:
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

shamansystems, 2021-04-03:
You can use IPA. I use 99% ipa. Just make sure the board is dry before power up

Closed 2021-04-05.

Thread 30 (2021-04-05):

Hall sensor positioning not vorking with howerboard motor

astra404, 2021-04-05:
Hello,
I tried to monitor the motor position by using hall efect sensors in 10" hoverboard motor (WT25HB36v20180408), but graph in vesc tool does not show anything. Can it be that vesc tool just not display this data (it shows im running in limited mode)? Or there is a probem somwhere else?

I mesured the signal from hall sensor with multimeter (gnd probe on gnd pin and sens probe on hall pin ) it shows 0.5v difrence when when I moove the motor. If it would help I can send a video and photos.

astra404, 2021-04-05:
Nevermind, after running hall efect sensor detection everything started to work fine. Also I didn't see the motor mode selection (it was set to sensorles :D).

Closed 2021-04-05.

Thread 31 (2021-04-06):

Max 5v current?  And other specs?

astra404, 2021-04-06:
What is max 5v current output of focer?
I am planing to use 5v output of the focer to power external mcu (arduino with atmega32u4) and other periferals like tft display.
Also it would be nice that there would be datasheet or spec paragraph for this kind of parameters (max 5v current output, min max voltages for gpio pins etc.)for the focer. If there is one sory for asking dumb questions :D.

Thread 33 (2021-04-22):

STM32F405RGT6/7 alternatives.

BigHuz, 2021-04-22:
Hello everyone so I have done a little research for ST microcontroller on cf2. I was  thinking to myself is it possible that STM32F407RGTxx would be a sutible alternative for microcontroller that is listed in cf2 bom. Also there is a STs paragraph that says that STM32F405xxxx and STM32F415xxxx are used in the same fields and have same specs. So STM32F407xxxx and STM32F405xxxx microcontrollers are from the same microcontroller lineup and STM32F415xxxx has same specs as listet ST microcontroller for cf2. Now which one of this above mentioned chips would you recommend for alternative chip and if possible and safe to use some copy cat chip form other companys (something like Giga Devices)?? Sorry if I have repeated myself I am very new to world of microcontrollers. Thanks in advance,
BigHuz

shamansystems, 2021-04-28:
The VESC project only supports one kind of MCU at the moment. This means the CFOC2 will only support this same MCU. No other substitutes are compatible.

BigHuz, 2021-04-28:
Not even STM32F305RGT7 the one with bigger working temperature range. Is so thank you very much.

shamansystems, 2021-04-28:
If the only difference is the operating temperature range, then I suppose it would work.

Closed 2021-04-28.

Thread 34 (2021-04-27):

200A / 12 FET version.

xromansx, 2021-04-27:
Hi,
 I was interested if there are any plans to build 200A version, 200 Amps means it will need 12 FETS and better cooling or everything is much more complicated ? I'm new to all this. Thanks

bj97301, 2021-04-27:
Yep. Feel free to checkout shaman's posts at the forum below:

https://forum.esk8.news/t/little-focer-84v-5kw-vesc-based-controller/50110/256

xromansx, 2021-04-27:
I saw it but it's only 75Amps and as I know that minimum for couple of month you wouldn't buy it OOS ... that's why I was thinking what can be done to Cheap FOCer to increase the amps ... or it there will be high A version I need it for 12S. Intend to use it with efoil.

bj97301, 2021-04-27:
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

xromansx, 2021-04-27:
I saw this prototipes before they look nice but as I know they where never realized.

bj97301, 2021-04-28:
Not yet. Little focer is being released slowly so soon enough.

xromansx, 2021-04-28:
Do you know if there are any schematics with 12 FETs interesting to see what FETs are used and how different is the scheme?

bj97301, 2021-04-28:
Probably not much. He's going more retail focused with the rest of the controllers.

shamansystems, 2021-04-28:
There aren't any existing schematics with 12 FETs or anything more powerful than the CFOC2 for open hardware. I do have plans for a more powerful CFOC3 in the future but that has not yet been started. You are more than welcome to alter the existing open source and available KICAD project files and create a 12 FET version for yourself.

xromansx, 2021-04-28:
Thanks for all your efort and time you are putiong in this project. Is your comercial version based on DRV8353RS  ? And CSD18536KCS and NCEP60T20 in their datasheet it tells that they can support 200A but in real life more then 50A geting them to hot is something else is limiting max Amps or with good cooling they can support much more? Regarding 12 FET I wanted to understand they are used in paralel to decrease RDS and to redistribute the heat.
Thanks

shamansystems, 2021-04-28:
The Little FOCer does use the  DRV8353RS and operates up to 84V with no problem.

The datasheet numbers for max current on MOSFETs is a very misleading number. Real life performance is much different and depends on system cooling.

Yes parallel MOSFETs reduce the total Rds(on) and therefore increase the total current that can be delivered.

xromansx, 2021-04-28:
Thanks for your reply, will be waining for your 12 FET version in meantime will try to experement with your cheap FOCer 2 maybe increasin nr of fets to see if can get to higher currents, this problem with parts shortage is also anoing.
Thanks.

shamansystems, 2021-04-28:
To be clear, I never said I was working on a 12 FET version. But indeed a more powerful version. More details on this after I have prototypes in the future.

Closed 2021-04-28.

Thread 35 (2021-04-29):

Replace drv8301 with drv8302

L4stIdi0t, 2021-04-29:
would it be possible to replace the drv8301 with a drv8302?

FFDamien, 2022-10-02:
hello,
8301 speak in SPI, and 8302 with GPIO.
No, that will not work.
Maybe a 8301Q ?

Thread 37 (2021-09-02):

out of stock parts

cloudsrule9, 2021-09-02:
I am trying to order a few cheap focer 2 for a couple of projects i am working on. I have used jlcpcb before for a few circuit boards, but i am having trouble with a number of parts that are currently out of stock.  Does anyone know of good alternatives for the following
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

I don't care about the BMI160, as this chip isn't required for my project, but the others seem to be rather important. My current idea is to just wait and see if they come back into stock, but i was wondering if anyone had any better ideas.

Cheers

vicgwee, 2021-09-09:
There have been several issues raised about the chip shortages as well: #29, #23, #24 to name a few.

Hopefully it won't persist much longer!

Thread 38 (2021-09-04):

is it possible to change mosfet n channel ncep60t20 to mosfet n channel irf3205

artayasa, 2021-09-04:
is it possible to change the n-channel mosfet ncep60t20 to the n-channel mosfet irf3205. because irf mosfet is much cheaper in my country.

zwn, 2021-10-04:
Have I found the correct references?

- https://lcsc.com/product-detail/MOSFET_Wuxi-NCE-Power-Semiconductor-NCEP60T20_C284868.html
- https://lcsc.com/product-detail/MOSFETs_Infineon-Technologies-IRF3205PBF_C2561.html

They seem similar enough. Has anyone tested it?

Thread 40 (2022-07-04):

Replacement of parts

snapo, 2022-07-04:
Heya....
First of all Thank you sooo much for all that work you have done.
i did want to order 5 and expected a 120$ price tag....
and got a little surprised. My Bill got to 300.50 USD .....

The most expensive thing is the
DRV8301DCAR , this costs 32.4 USD a piece because of the current global shortage. This price isnt worth the silicone inside it.
the cheaper chinese alternative is the DRV8301DCA (same pinout size, but 4 have to get a new trace) and costs only 7USD
Another alternative is is a different driver all together instead of TI.

Another way to make it way cheaper is replace the expensive STM32 (11USD piece) with a raspberry pi pico ... both of them run at 168Mhz but the pico chip is 80% less expensive :-) jlpcb also has it in their smt service.

Best regards keep up the good work

Koxx3, 2022-07-04:
running vesc on rpi ?! good luck ! 😅

shamansystems, 2022-07-05:
Hey there. I'm working on the CFOC3 right now to address the current shortages and also improve performance. No more DRV. Still has the STM32 since the VESC firmware only runs on that.

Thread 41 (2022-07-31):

Updated BOM

DFlak, 2022-07-31:
Hey, just finished ordering parts for CFOC, I went line by line looking for cheaper alternatives, this bom doesn't have STM, DRV, CAN-Bus chips and the IMU since I'm sourcing them from broken drones lol. Quantities are for 5 units of CFOC boards.
Attached is my fresh BOM, hope this helps someone.
[LCSC_Exported_20220731.csv](https://github.com/shamansystems/Cheap-FOCer-2/files/9228842/LCSC_Exported_20220731.csv)

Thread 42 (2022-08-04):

Error in the assembly readme.md for diode placement

Richie6988, 2022-08-04:
Just to let you know guys so you avoid doing the same mistake I did...

In the guides/assembly readme.md, you find the following mention :

**Semi-complete white rectangle silkscreen marking around diode. The absent side of the rectangle marks the Cathode(negative). The other side is the Anode(positive) as shown below**

Actually, this is the opposite. You have to **place the Anode on the absent side of the rectangle marks**. This is particularly important for the V1.0 version with a lot of diodes ;)

Cheers

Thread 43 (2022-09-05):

Safe to leave out BMI160 attitude sensors?

wait-what, 2022-09-05:
BMI160 costs €5.4547 a piece at the moment, so I was wondering if it's safe to just leave it's spot empty if I have no plans for using it?

AntumArk, 2022-09-12:
Well if you leave out all of the required components for it as in [BMI160 datasheet](https://www.mouser.com/datasheet/2/783/BST-BMI160-DS000-1509569.pdf) and configure firmware so it would not use it, then it should be fine. The same thing is often done with MPU6050 which is also I2C device.

wait-what, 2022-11-30:
Thank you

Closed 2022-11-30.

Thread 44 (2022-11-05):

STM32 Placement Rotation unclear

NiklasProbst, 2022-11-05:
I have a Problem with the STM32.

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
In the Official Assembly Image above the stm32 is facing downwards.

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
Here is the official Pinout for the STM32 F405 LPFQ

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
This is a Screenshot from the Cheap Focer 2 in KiCad. According to the PINs in KICAD and the STM32 Datasheet, the right placement would be a 90° rotation to the right. However, in the official Assembly instructions it's rotatet 180°.
Can somebody help me what's the right placement?
Thank's in advance,
Niklas

NiklasProbst, 2022-11-06:
Could figure it out myself. The inscription official PINout Diagram for the STM32F40xx is 90° turned, so you can't use this for orientation. Instead take a look at this:

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

Use the little dot as a reference point.

Closed 2022-11-06.

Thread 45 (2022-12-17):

NOOB question: I cant find any 2W version of R57-R61 on LCSC/JLCPCB.

Meserlion, 2022-12-17:
Can i use 1W instead? Or can i use 2X1w to get the same? This is the first time im ordering any kind of PCB. Your guide is amazing BTW.

Meserlion, 2022-12-17:
C2931966, This is the only 3W i can find. Will that work?

charclo, 2022-12-17:
That will probably work. It should be a 2512 resistor with 1mOhm and at least 2W.
Make sure to order the 1.0 version of the cheap focer 2, it is in the developer branch. Also, Shaman is working on a cheap focer 3 with some improvements. If you don’t need it soon, you can wait for that

Meserlion, 2022-12-17:
So... what happens if i already ordered 0.9?

charclo, 2022-12-17:
Not that much, there were some small improvements. Just make sure to use the firmware for 0.9 version. It is included in the latest vesc tool, or the firmware included in the github repo of the cheap focer 2

Meserlion, 2022-12-17:
Thanks, i think ill use 0.9 for making all my mistakes on. Then i can upgrade to v3 when that is ready.

charclo, 2022-12-17:
👍

charclo, 2022-12-17:
👍

Meserlion, 2023-01-27:
Its alive! I connected to VESC tool and MCU is responding fine.

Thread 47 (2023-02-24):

question about replacement

okhsunrog, 2023-02-24:
can I use mosfets IRFB7530PBF?

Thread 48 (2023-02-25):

Update links

okhsunrog, 2023-02-25:
https://github.com/shamansystems/Cheap-FOCer-2/blob/Developer-Branch/guides/assembly/partsList.md
A lot of links are not working and I don't even understand what pin headers I need. Please help.
In my turn I'm ready to help with monitoring lcsc and updating BOM from time to time

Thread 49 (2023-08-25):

5V voltage issue

Tank1989, 2023-08-25:
When I first used this board, I only provided 5V voltage with a regulated power supply. Why is the current high and the voltage less than 5V? What is the reason for this?

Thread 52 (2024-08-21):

problem with missing parts from the Bom or CPL file

asken92, 2024-08-21:
Hello awsome project!

I tried to followed the ordering guide, but im getting error with either the BOM or CPL file for missing parts. Se image
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

(The below parts won't be assembled due to data missing.
Q1,Q2,Q3,Q4,Q5,Q6,J1,J2,J3,J4,J5,USB1,P4,P5,C39,C38 designators don't exist in the CPL file.)

anyone knows whats wrong or if its correct and how i can proceeed?

much thanks!

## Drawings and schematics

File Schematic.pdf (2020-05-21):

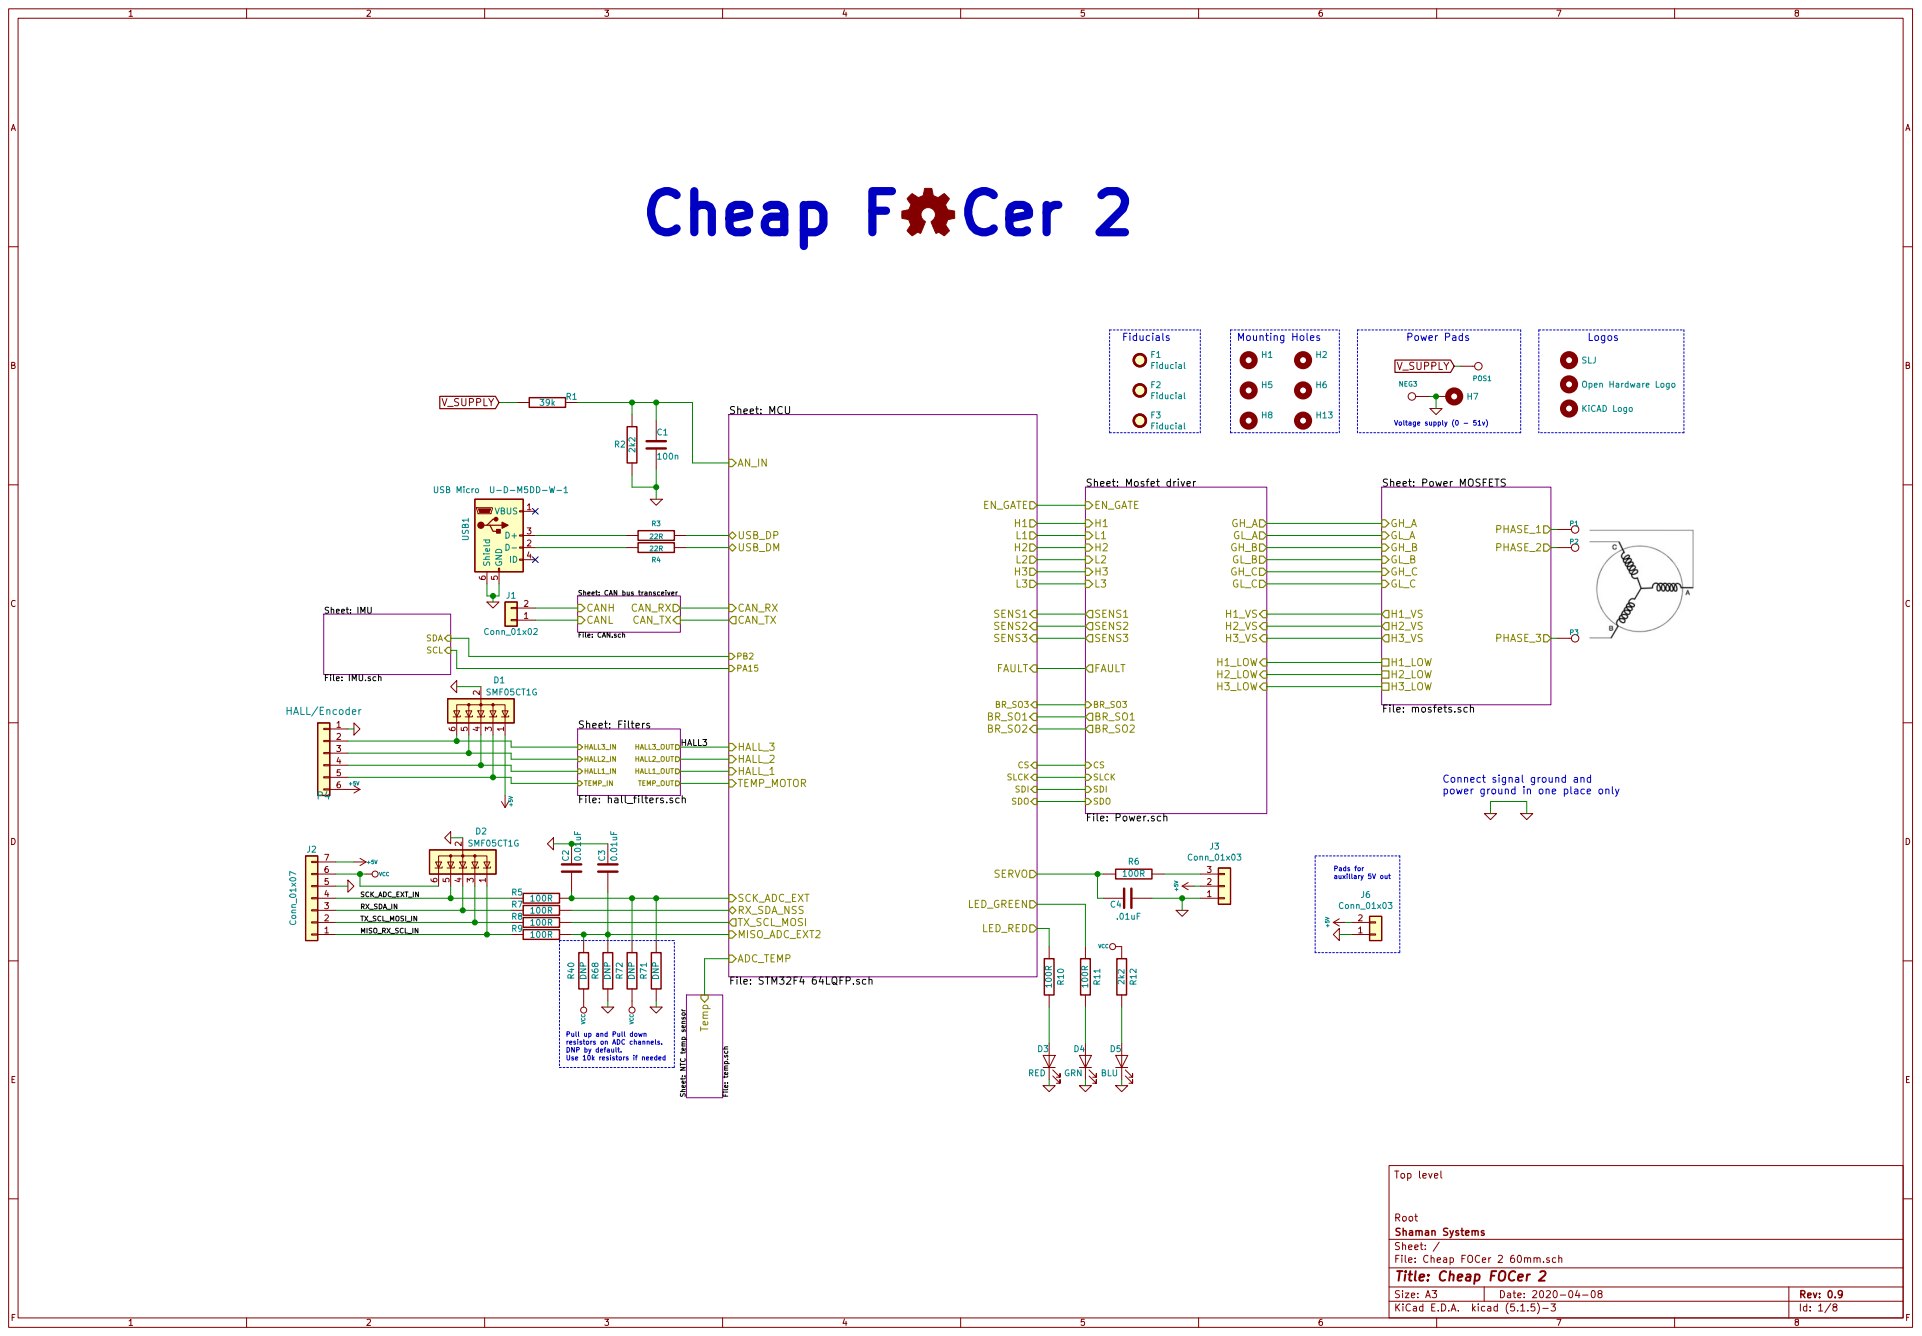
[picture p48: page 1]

power ground in one place only

Pull up and Pull down resistors on ADC channels. DNP by default. Use 10k resistors if needed

File: Cheap FOCer 2 60mm.sch Sheet: / Shaman Systems Root Top level

Id: 1/8 Title: Cheap FOCer 2

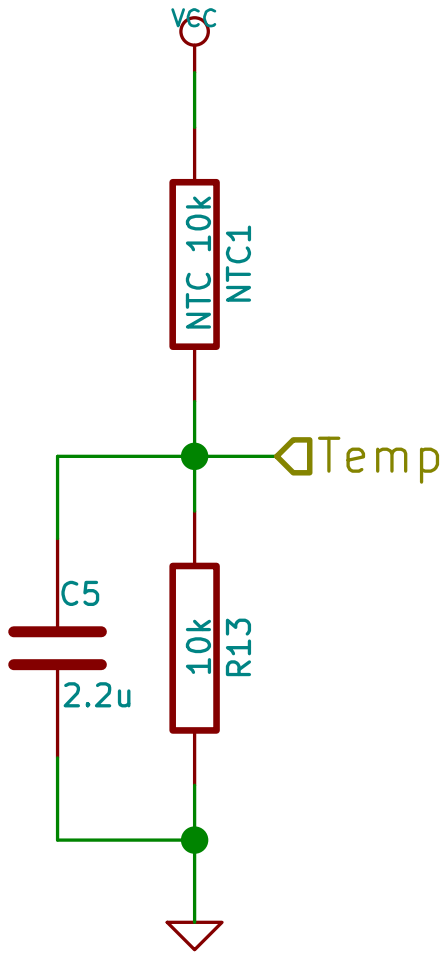
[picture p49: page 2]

Shaman Systems Root Top level 10k R13 C5

Sheet: /NTC temp sensor/
File: temp.sch
Id: 2/8 Title: Cheap FOCer 2

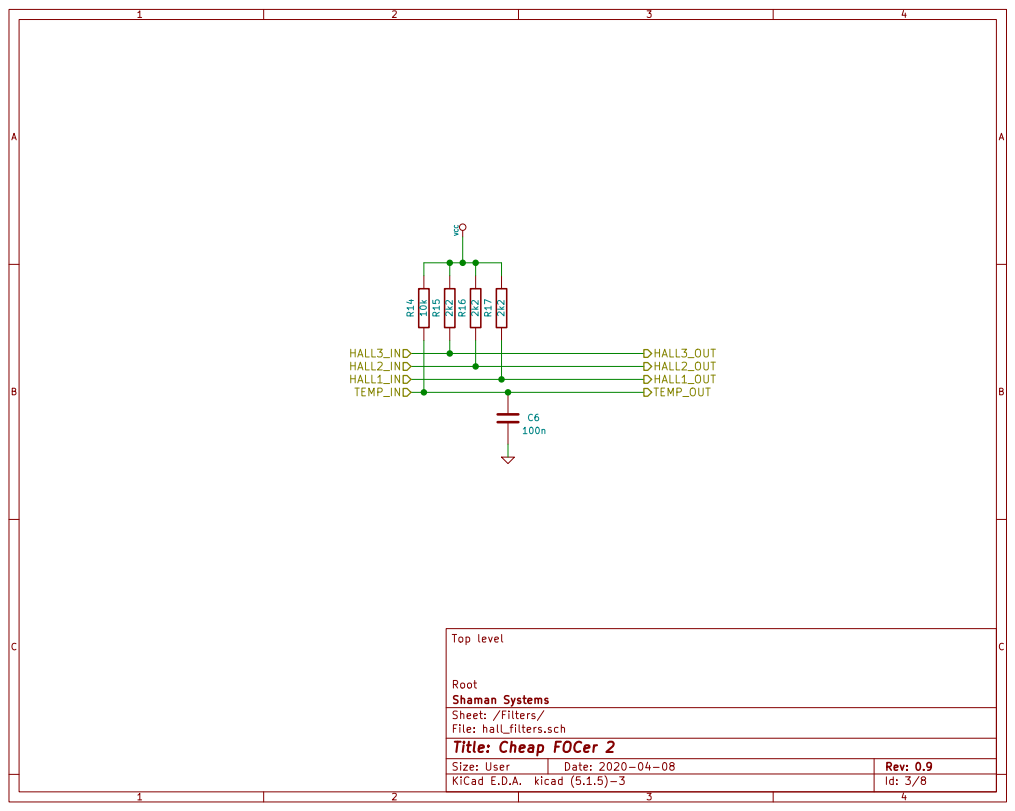
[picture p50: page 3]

Id: 3/8 Title: Cheap FOCer 2

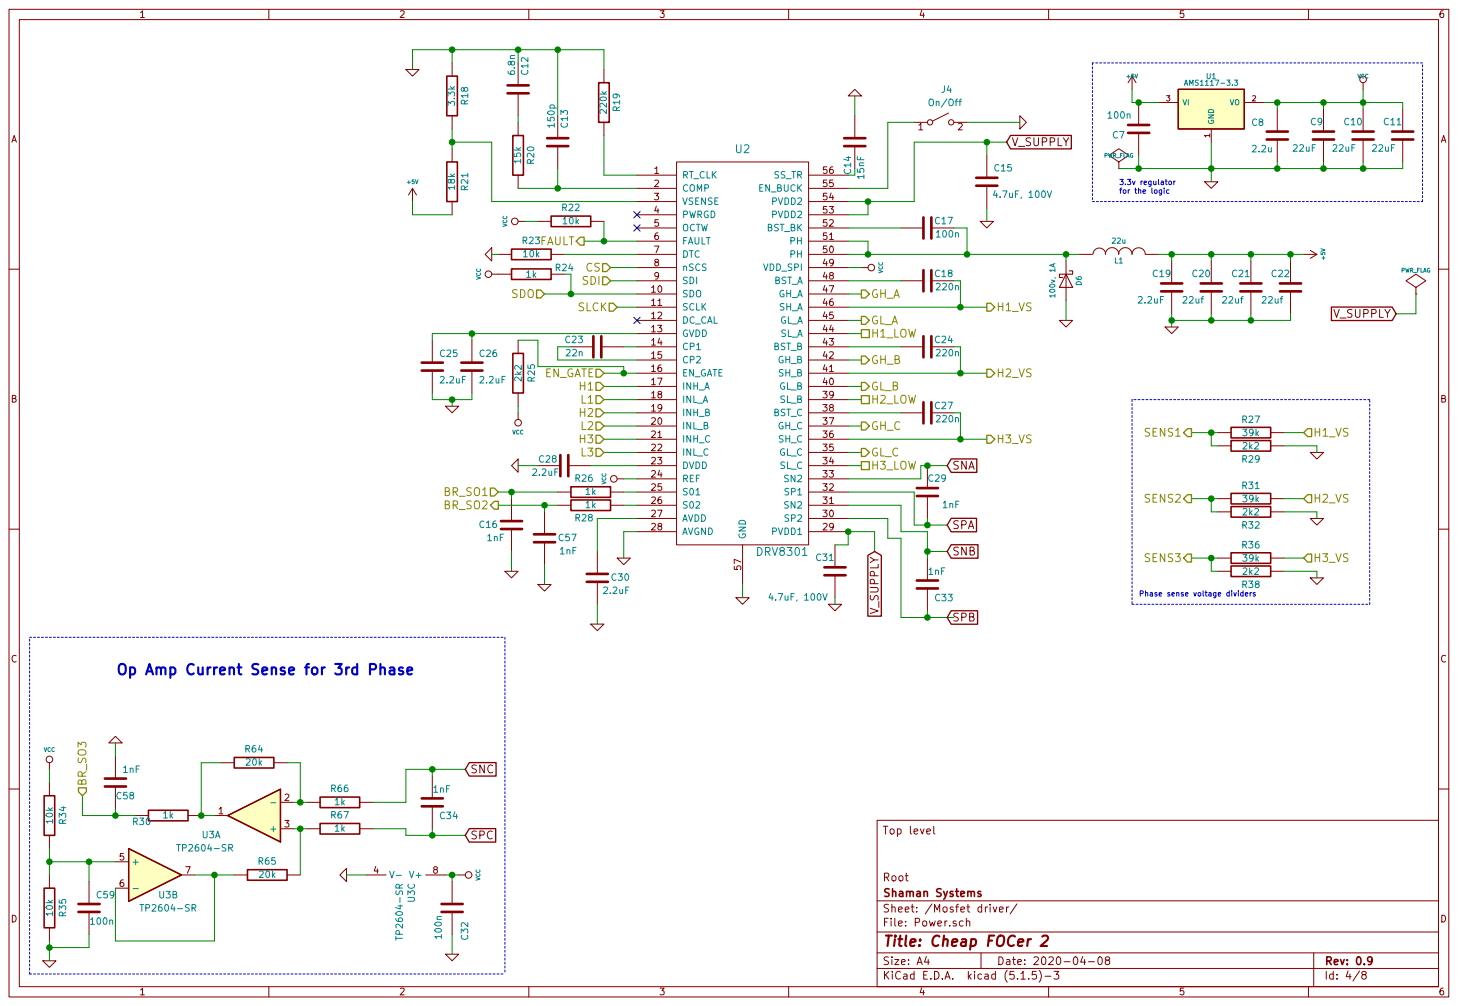
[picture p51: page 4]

for the logic Phase sense voltage dividers Op Amp Current Sense for 3rd Phase

File: Power.sch Sheet: /Mosfet driver/ Shaman Systems Root Top level VCC R67

Id: 4/8 Title: Cheap FOCer 2

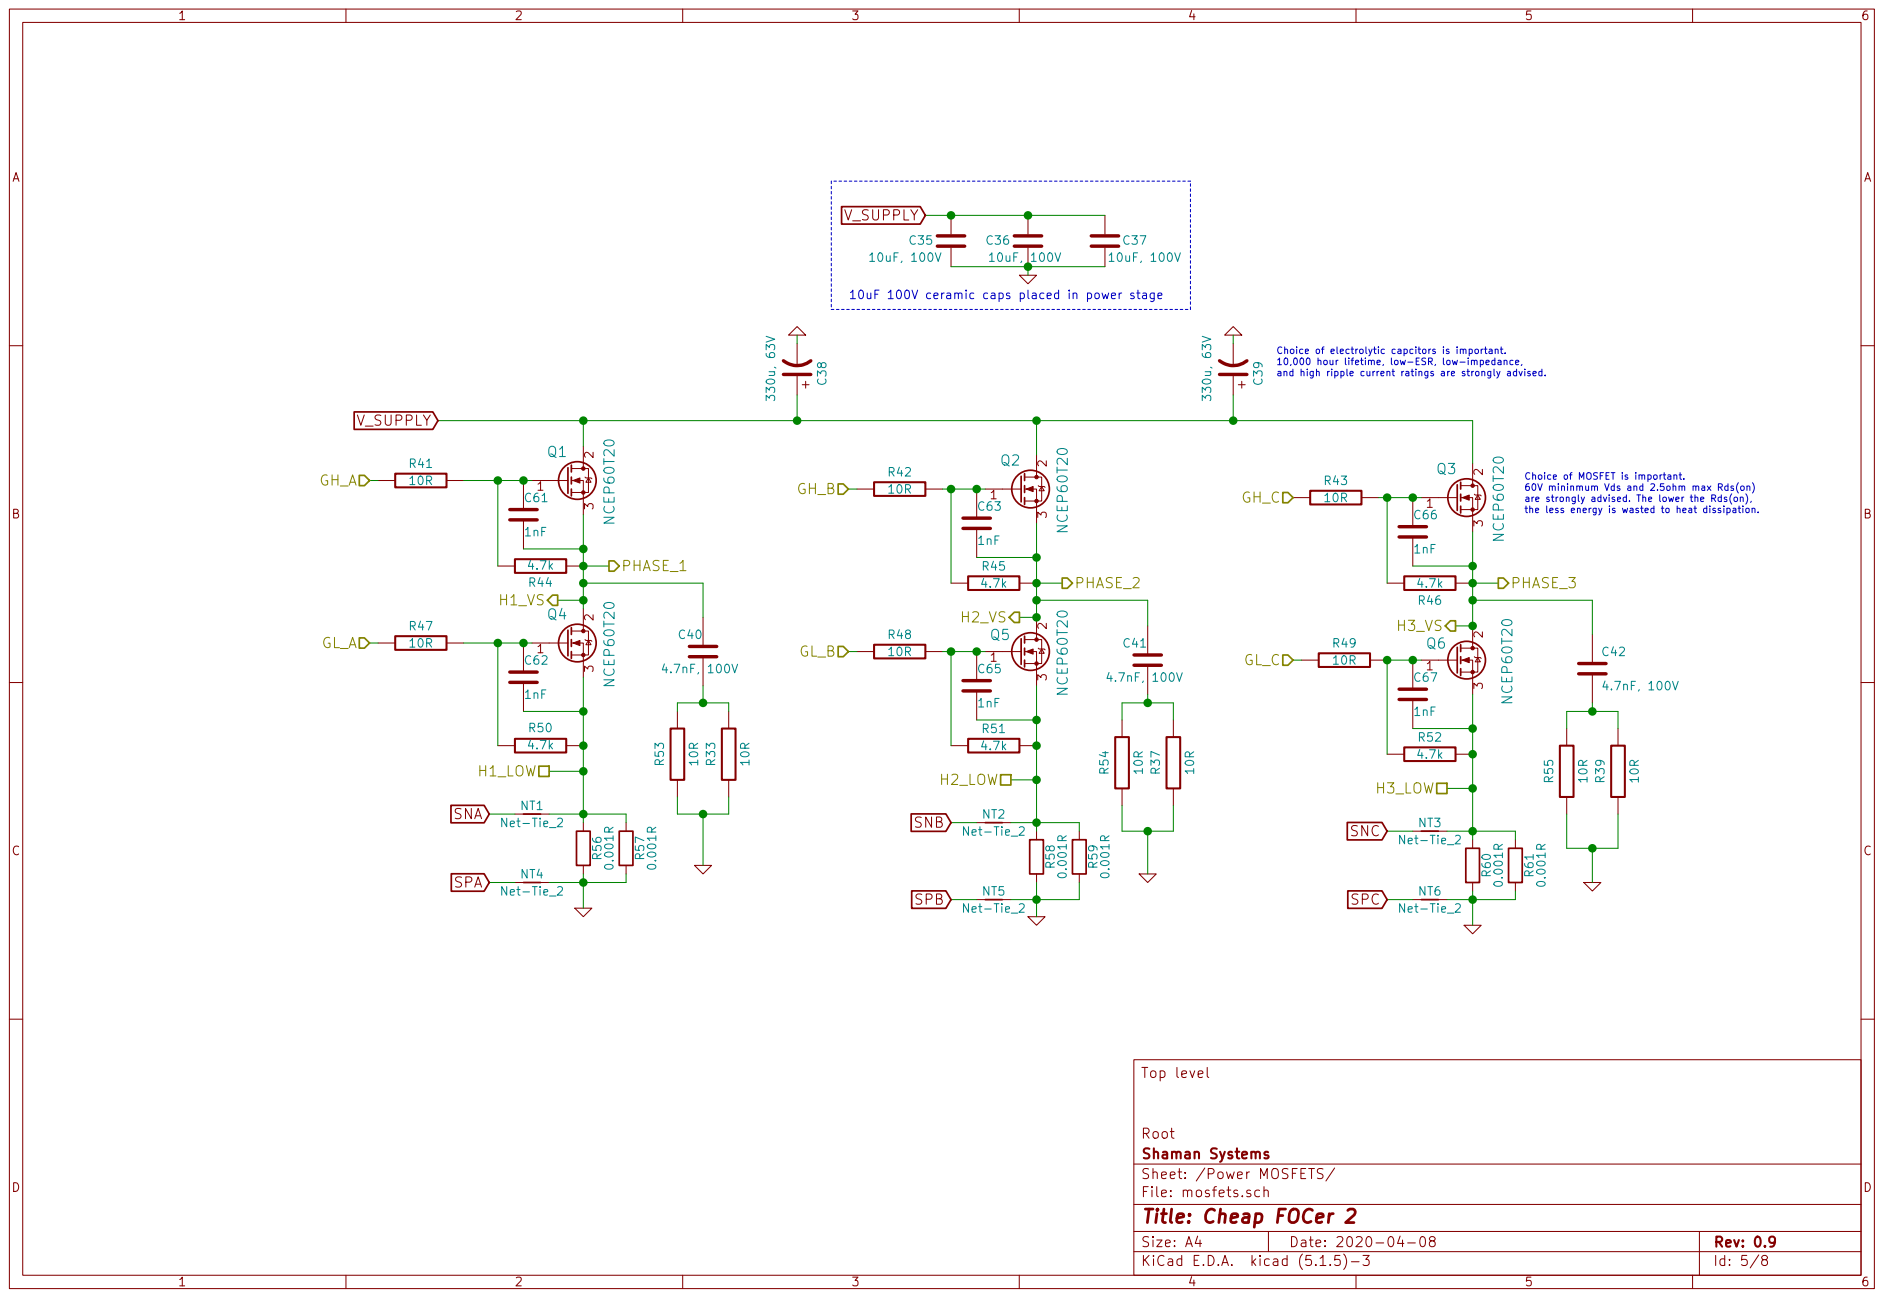
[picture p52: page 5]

the less energy is wasted to heat dissipation.

Id: 5/8 Title: Cheap FOCer 2

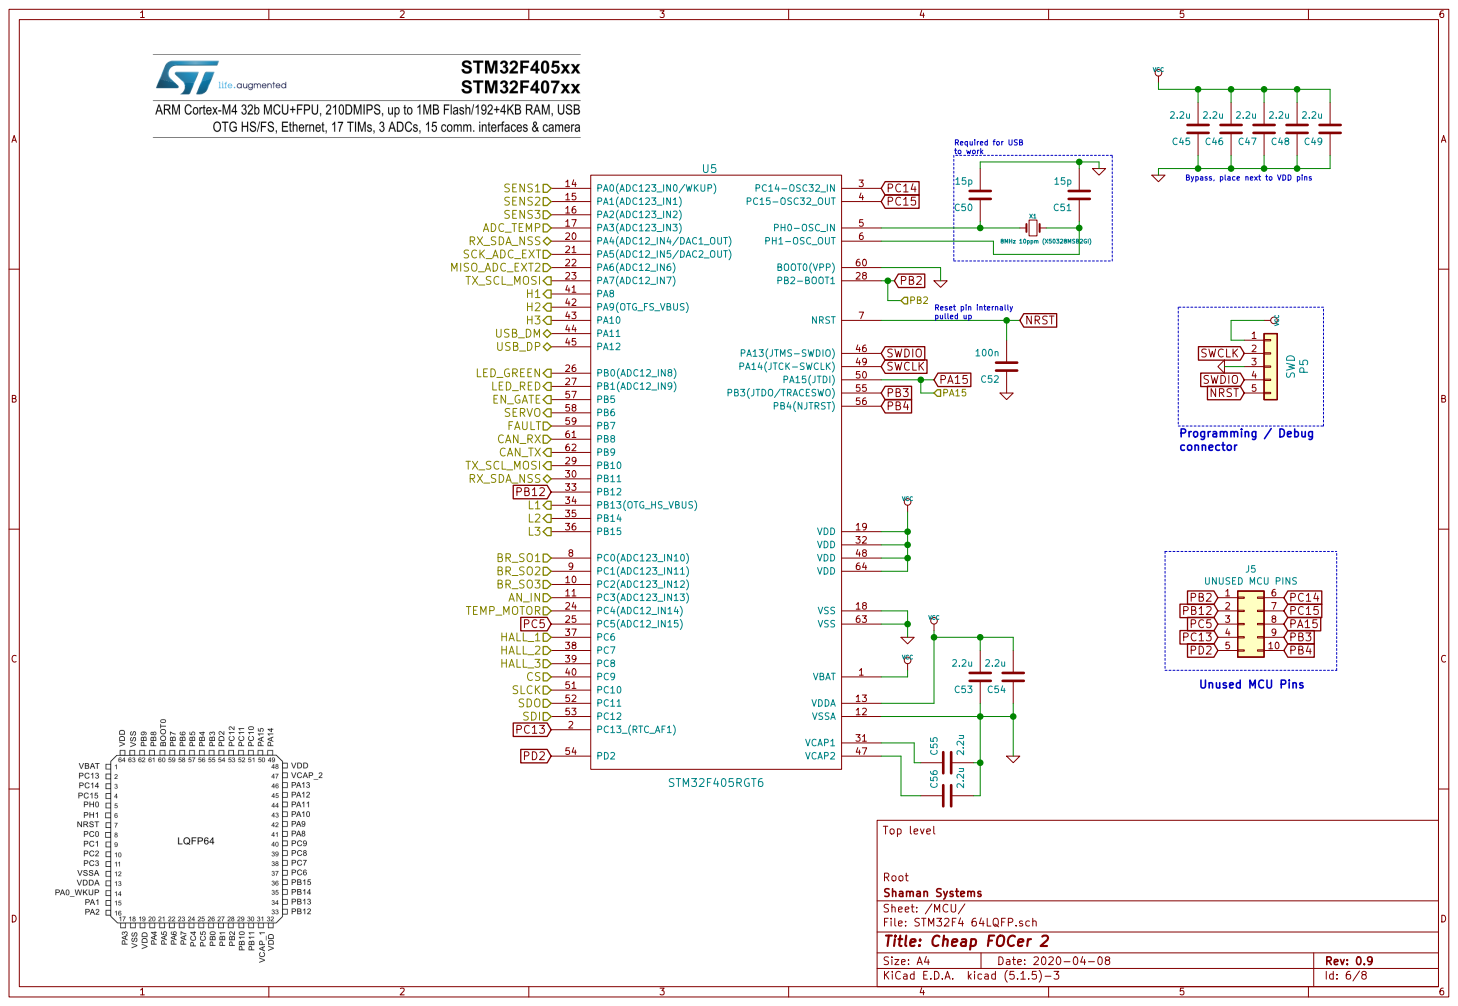
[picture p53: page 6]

Bypass, place next to VDD pins Required for USB

connector Reset pin internally pulled up

Id: 6/8 Title: Cheap FOCer 2

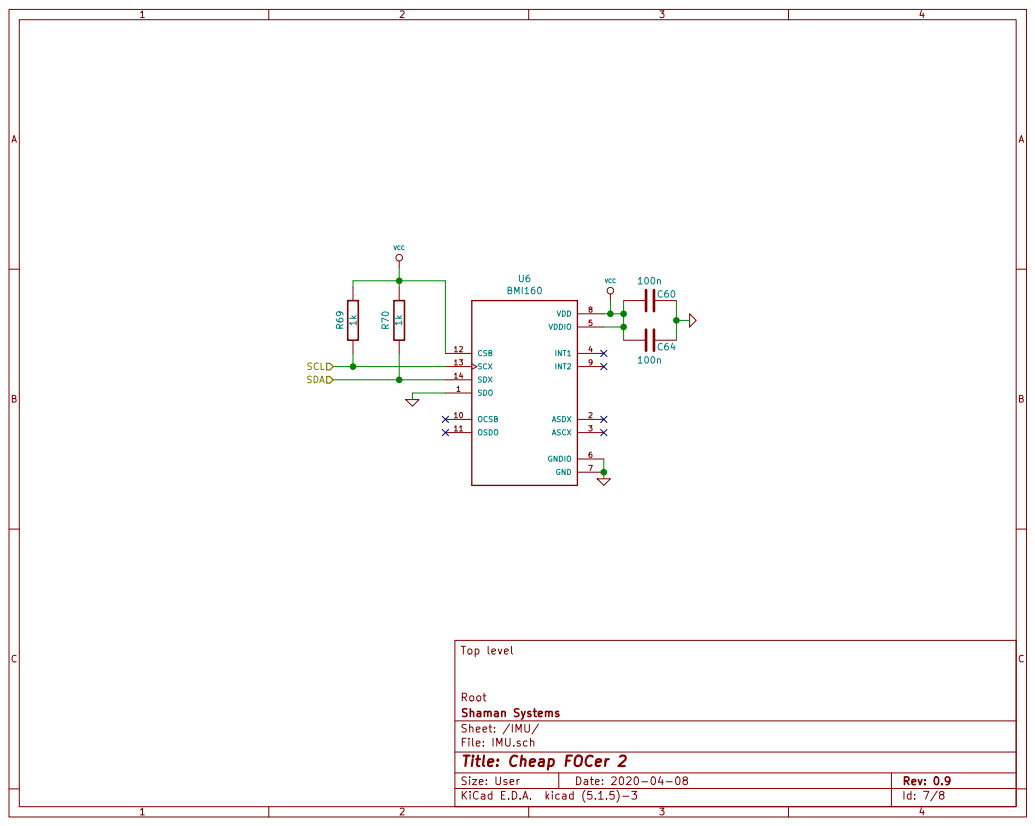
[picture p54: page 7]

Id: 7/8 Title: Cheap FOCer 2

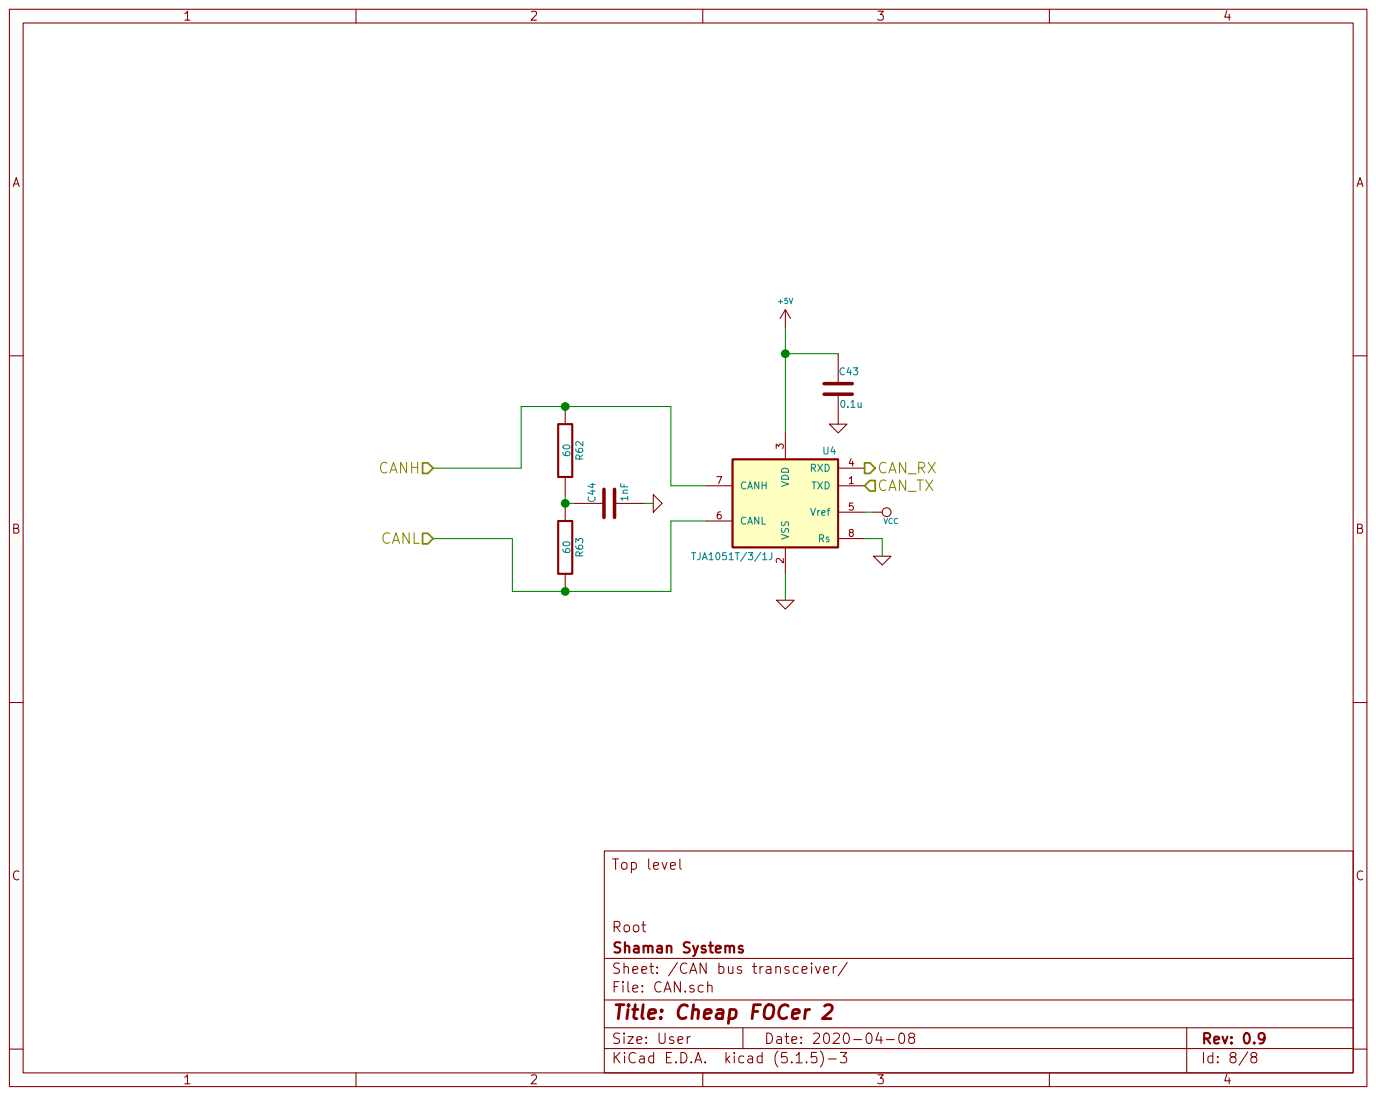
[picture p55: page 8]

3 RXD 4 Vref 5 CANL 6 CANH 7 Rs 8 U4 TJA1051T/3/1J CAN_RX

Id: 8/8 Title: Cheap FOCer 2

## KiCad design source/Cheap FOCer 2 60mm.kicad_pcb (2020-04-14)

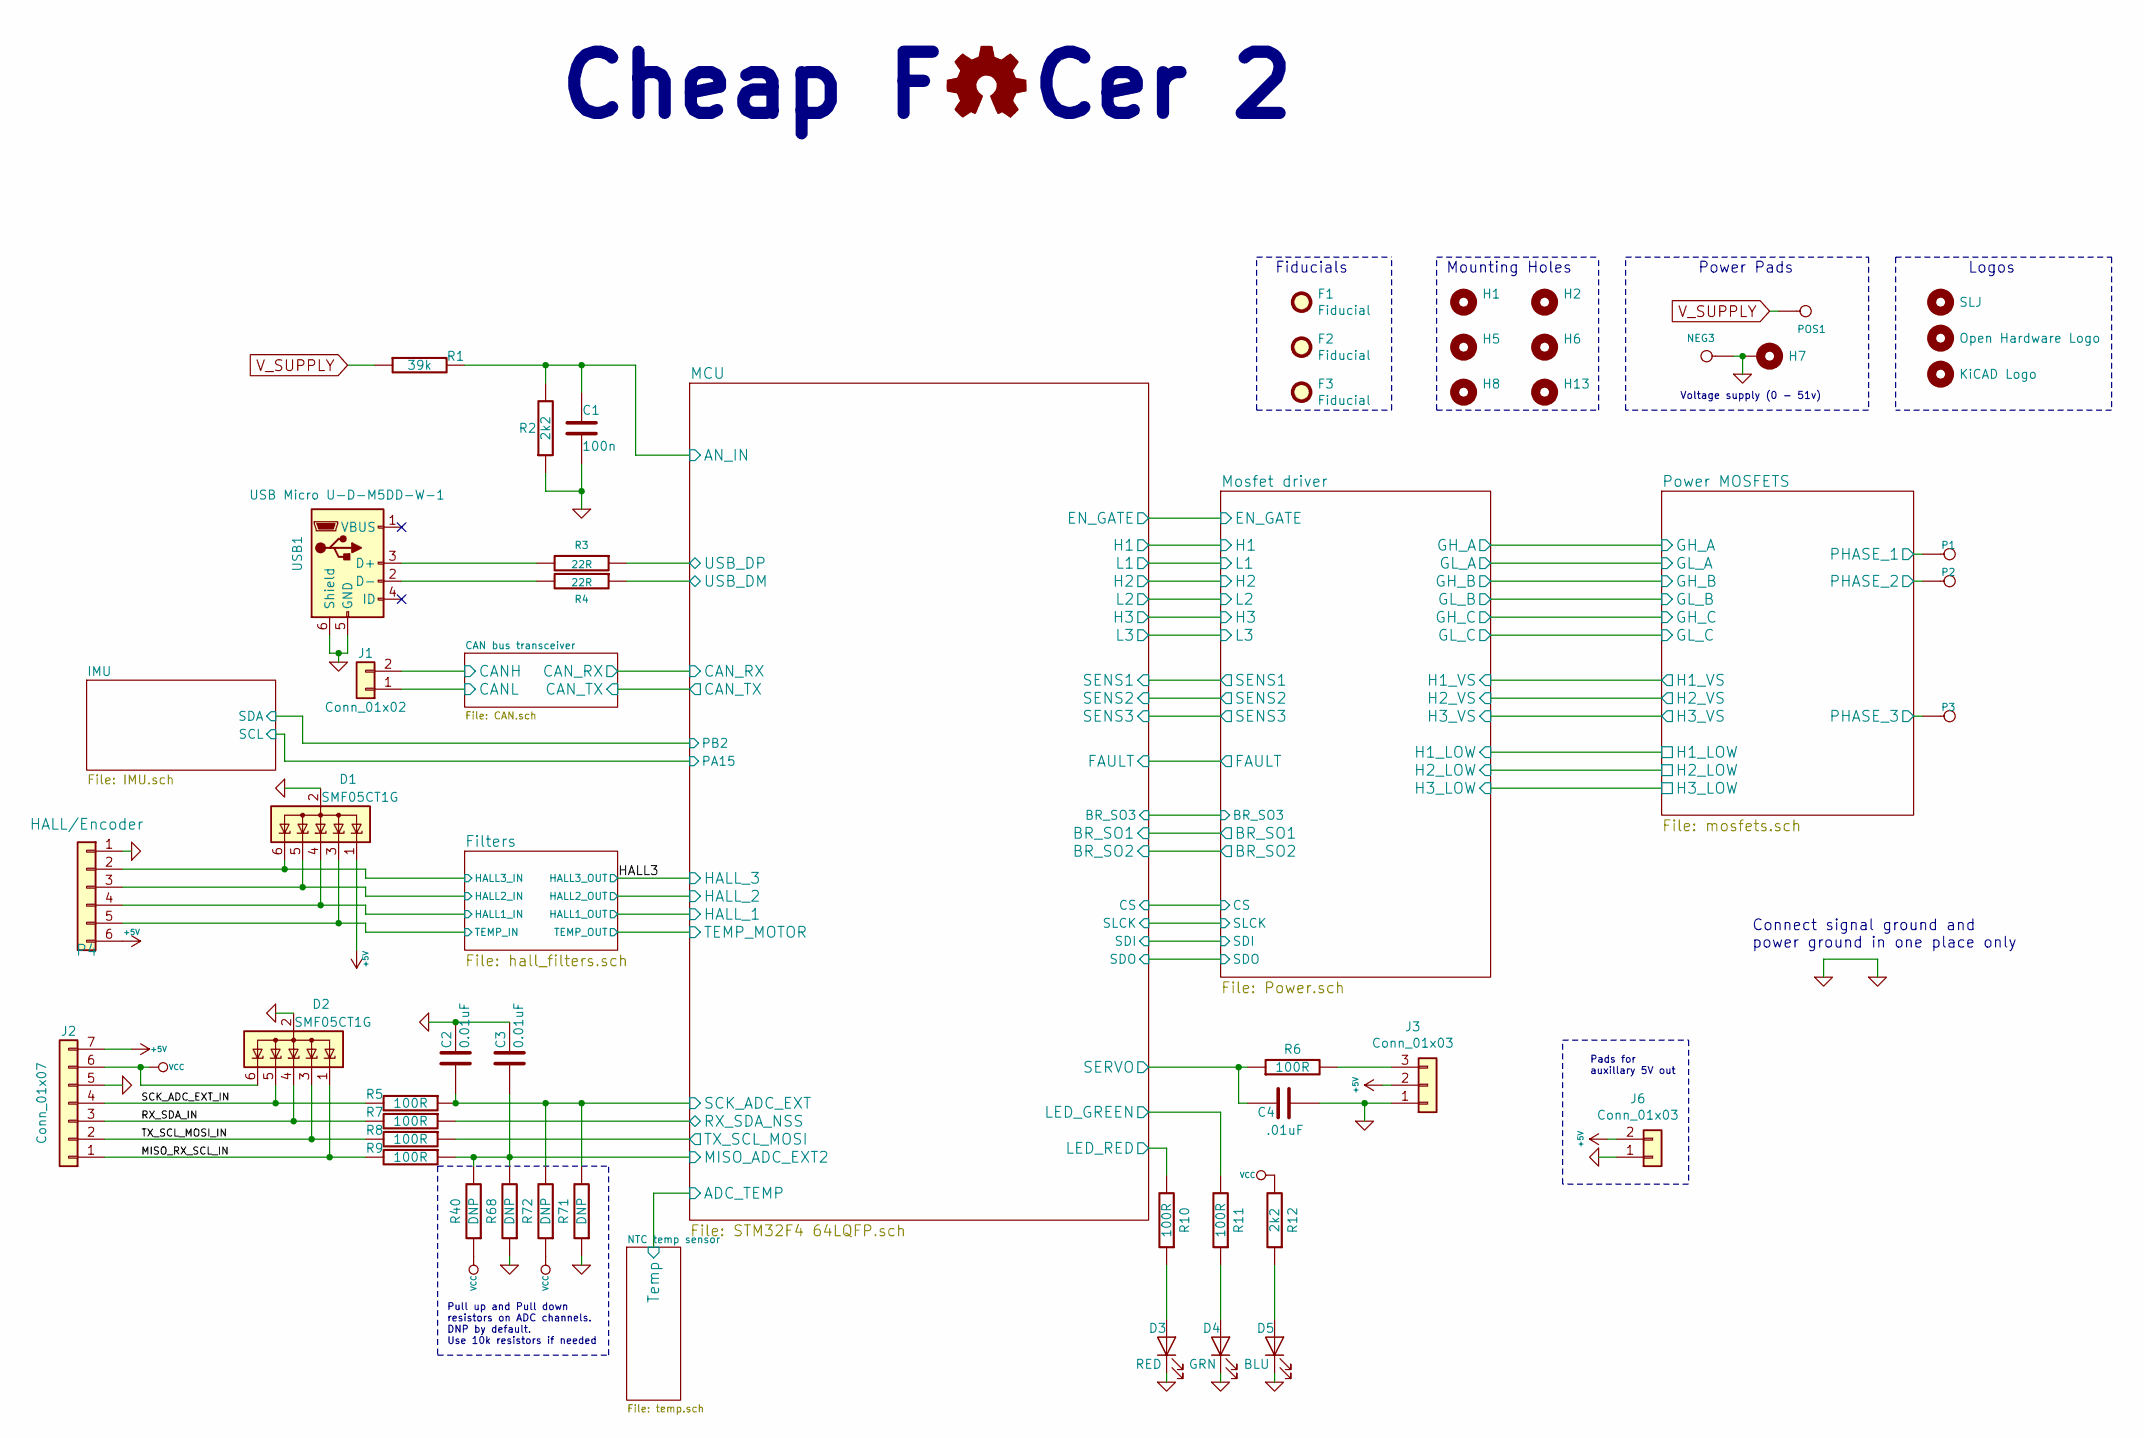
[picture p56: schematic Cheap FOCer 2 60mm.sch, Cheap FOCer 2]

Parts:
C1: 100n; C_0603_1608Metric
C2, C3: 0.01uF; C_0603_1608Metric
C4: .01uF; C_0603_1608Metric
D1, D2: SMF05CT1G; SOT-363_SC-70-6
D3: RED; LED_0603_1608Metric
D4: GRN; LED_0603_1608Metric
D5: BLU; LED_0603_1608Metric
F1, F2, F3: Fiducial; Fiducial_1mm_Dia_2mm_Outer
H1, H2, H5, H6, H7, H8, H13: MountingHole; MountingHole_3.2mm_M3_ISO14580_Pad
H3: SLJ; Sam_J
H4: Open Hardware Logo; OSHW-Logo2_9.8x8mm_SilkScreen
H9: KiCAD Logo; KiCad-Logo2_5mm_SilkScreen
J1: Conn_01x02; JST_PH_B2B-PH-K_1x02_P2.00mm_Vertical
J2: Conn_01x07; JST_PH_B7B-PH-K_1x07_P2.00mm_Vertical
J3: Conn_01x03; JST_PH_B3B-PH-K_1x03_P2.00mm_Vertical
J6: Conn_01x03; PinHeader_1x02_P2.54mm_Vertical
NEG3: MOTOR3; 1pin_4mm
P1, P2, P3: MOTOR1; 1pin_4mm
P4: HALL/Encoder; JST_PH_B6B-PH-K_1x06_P2.00mm_Vertical
POS1: POS; 1pin_4mm
R1: 39k; R_0603_1608Metric
R2, R12: 2k2; R_0603_1608Metric
R3, R4: 22R; R_0603_1608Metric
R5, R6, R7, R8, R9, R10, R11: 100R; R_0603_1608Metric
R40, R68, R71, R72: DNP; R_0603_1608Metric
USB1: USB Micro U-D-M5DD-W-1; USB_Micro-B_Wuerth_614105150721_Vertical

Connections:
+5V: D1.1 (K), J2.7, J3.2, J6.2, P4.6; also elsewhere on the board
/CAN bus transceiver/CANH: J1.2; also elsewhere on the board
/CAN bus transceiver/CANL: J1.1; also elsewhere on the board
/Filters/HALL1_IN: D1.4 (K), P4.4; also elsewhere on the board
/Filters/HALL2_IN: D1.5 (K), P4.3; also elsewhere on the board
/Filters/TEMP_IN: D1.3 (K), P4.5; also elsewhere on the board
/HALL3: D1.6 (K), P4.2; also elsewhere on the board
/MCU/AN_IN: C1.2, R1.2, R2.2; also elsewhere on the board
/MCU/LED_GREEN: R11.2; also elsewhere on the board
/MCU/LED_RED: R10.2; also elsewhere on the board
/MCU/MISO_ADC_EXT2: C3.2, R9.1, R40.2, R68.2; also elsewhere on the board
/MCU/RX_SDA_NSS: R7.1; also elsewhere on the board
/MCU/SCK_ADC_EXT: C2.2, R5.1, R71.2, R72.2; also elsewhere on the board
/MCU/SERVO: C4.2, R6.1; also elsewhere on the board
/MCU/TX_SCL_MOSI: R8.1; also elsewhere on the board
/MCU/USB_DM: R4.1; also elsewhere on the board
/MCU/USB_DP: R3.1; also elsewhere on the board
/MISO_RX_SCL_IN: D2.1 (K), J2.1, R9.2
/Mosfet driver/H1_VS: P1.1; also elsewhere on the board
/Mosfet driver/H2_VS: P2.1; also elsewhere on the board
/Mosfet driver/H3_VS: P3.1; also elsewhere on the board
/RX_SDA_IN: D2.4 (K), J2.3, R7.2
/SCK_ADC_EXT_IN: D2.5 (K), J2.4, R5.2
/TX_SCL_MOSI_IN: D2.3 (K), J2.2, R8.2
unnamed: D3.2 (A), R10.1
unnamed: D4.2 (A), R11.1
unnamed: D5.2 (A), R12.1
unnamed: J3.3, R6.2
unnamed: R3.2, USB1.3 (D+)
unnamed: R4.2, USB1.2 (D-)
V_SUPPLY: POS1.1, R1.1; also elsewhere on the board

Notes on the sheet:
Voltage supply (0 - 51v)
Mounting Holes
Power Pads
Connect signal ground and power ground in one place only
Logos
Fiducials
Pull up and Pull down resistors on ADC channels. DNP by default. Use 10k resistors if needed
Pads for auxillary 5V out
Cheap F Cer 2

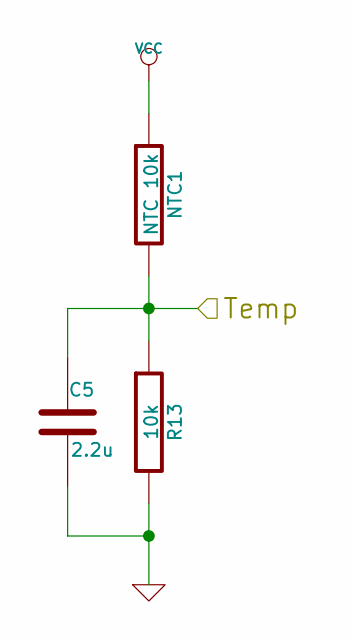
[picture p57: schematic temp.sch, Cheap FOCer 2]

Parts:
C5: 2.2u; C_0603_1608Metric
NTC1: NTC 10k; R_0603_1608Metric
R13: 10k; R_0603_1608Metric

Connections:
/MCU/ADC_TEMP: C5.1, NTC1.2, R13.1; also elsewhere on the board

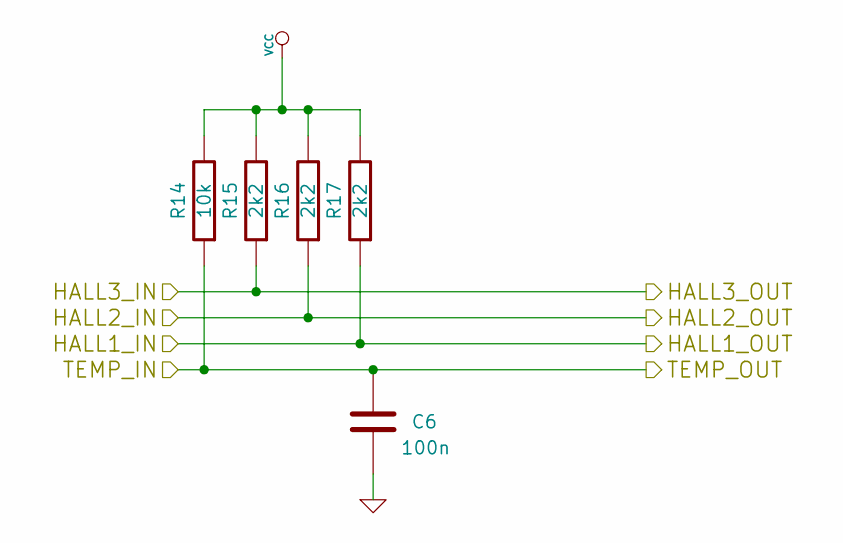
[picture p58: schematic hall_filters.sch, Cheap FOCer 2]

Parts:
C6: 100n; C_0603_1608Metric
R14: 10k; R_0603_1608Metric
R15, R16, R17: 2k2; R_0603_1608Metric

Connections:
/Filters/HALL1_IN: R17.1; also elsewhere on the board
/Filters/HALL2_IN: R16.1; also elsewhere on the board
/Filters/TEMP_IN: C6.2, R14.1; also elsewhere on the board
/HALL3: R15.1; also elsewhere on the board

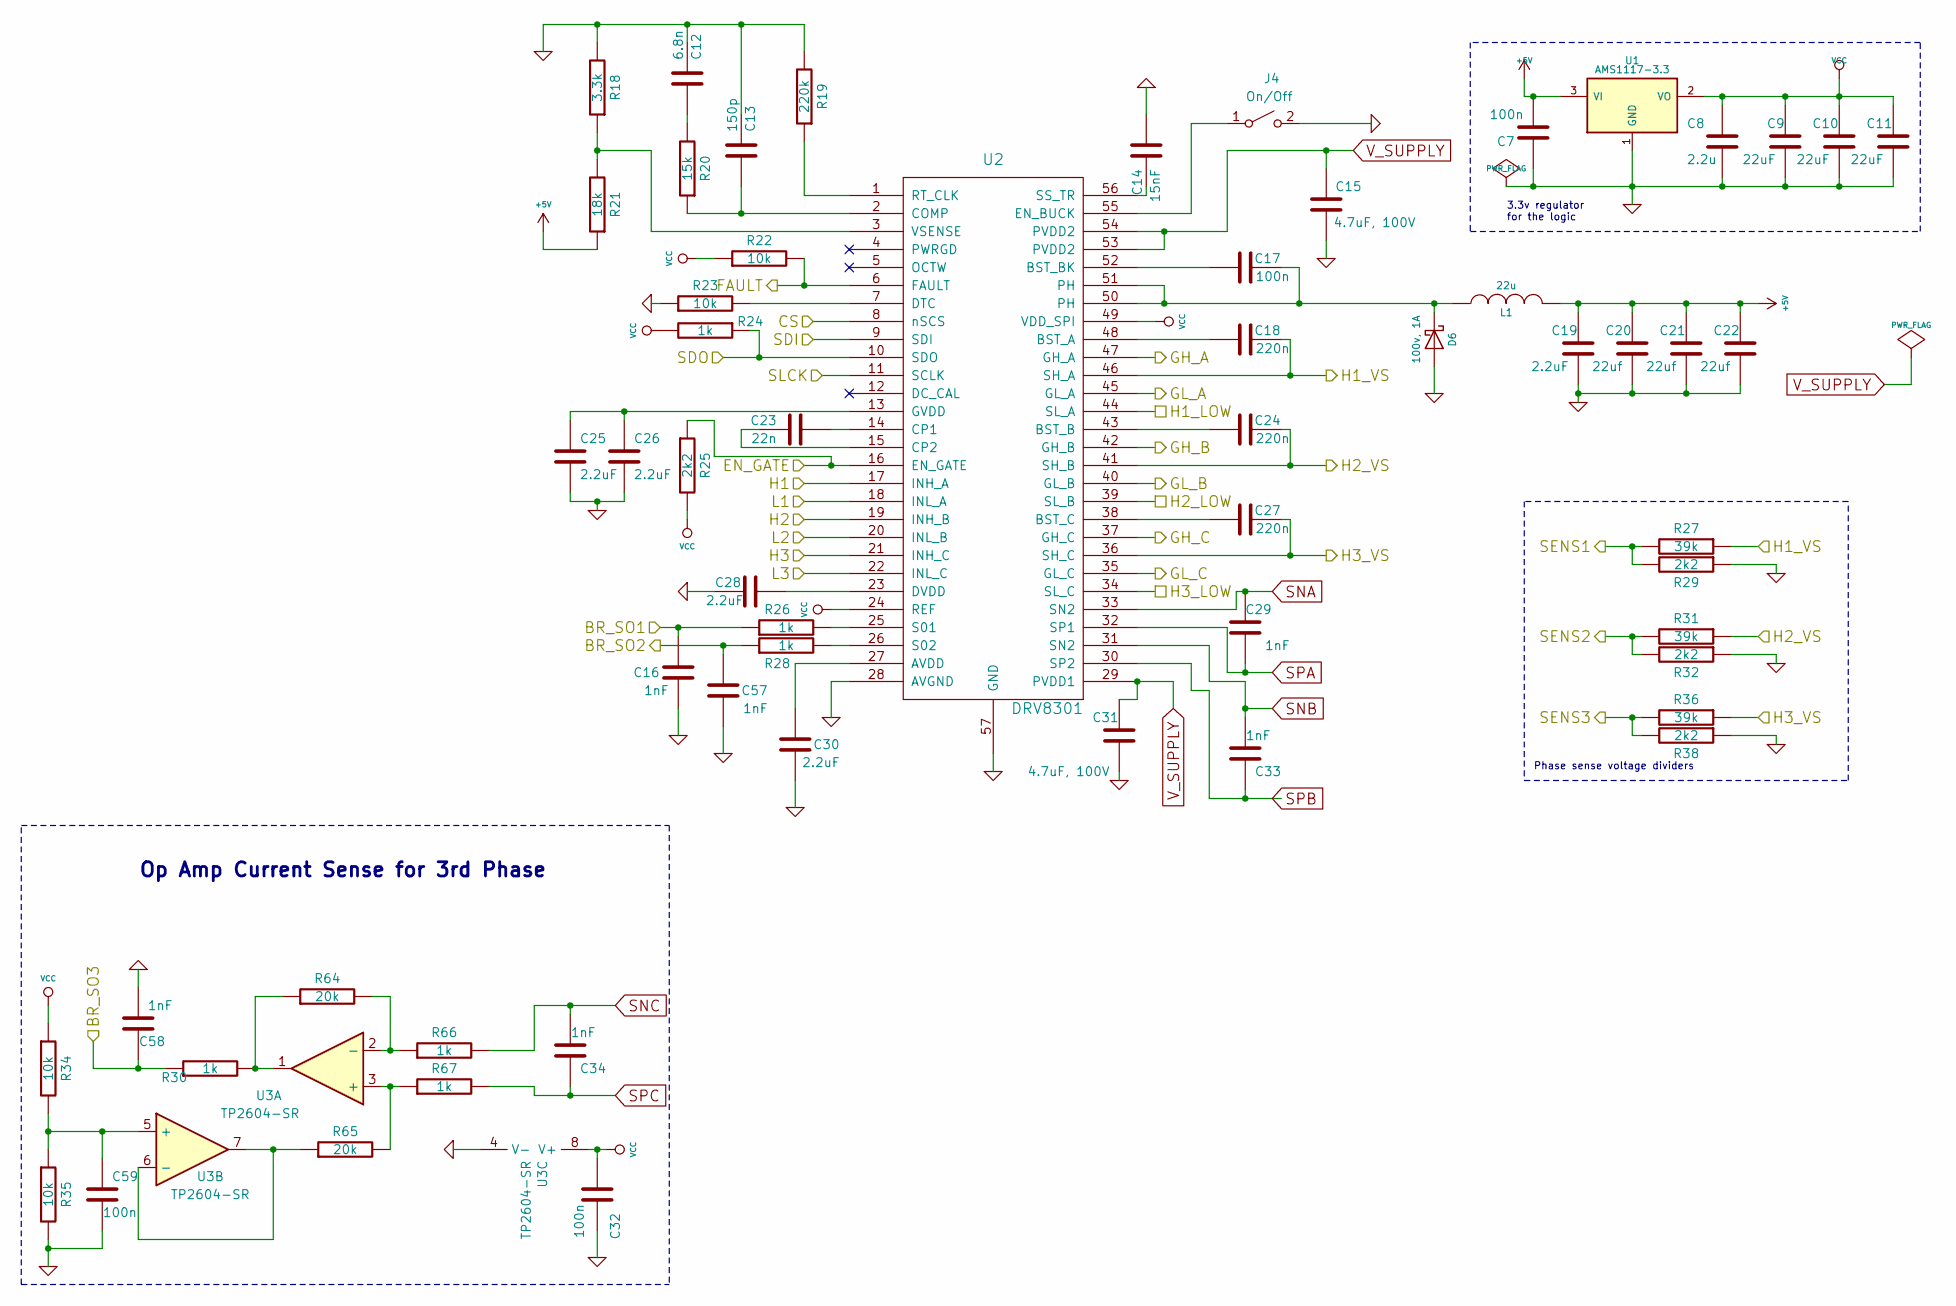
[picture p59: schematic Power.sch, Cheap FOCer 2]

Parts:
C7, C17, C32, C59: 100n; C_0603_1608Metric
C8: 2.2u; C_0603_1608Metric
C9, C10, C11: 22uF; C_0805_2012Metric
C12: 6.8n; C_0603_1608Metric
C13: 150p; C_0603_1608Metric
C14: 15nF; C_0603_1608Metric
C15, C31: 4.7uF, 100V; C_1210_3225Metric
C16, C29, C33, C34, C57, C58: 1nF; C_0603_1608Metric
C18, C24, C27: 220n; C_0603_1608Metric
C19, C25, C26, C28, C30: 2.2uF; C_0603_1608Metric
C20, C21, C22: 22uf; C_0805_2012Metric
C23: 22n; C_0603_1608Metric
D6: 100v, 1A; D_SMA
J4: On/Off; JST_PH_B2B-PH-K_1x02_P2.00mm_Vertical
L1: 22u; L_Taiyo-Yuden_NR-60xx_HandSoldering
R18: 3.3k; R_0603_1608Metric
R19: 220k; R_0603_1608Metric
R20: 15k; R_0603_1608Metric
R21: 18k; R_0603_1608Metric
R22, R23, R34, R35: 10k; R_0603_1608Metric
R24, R26, R28, R30, R66, R67: 1k; R_0603_1608Metric
R25, R29, R32, R38: 2k2; R_0603_1608Metric
R27, R31, R36: 39k; R_0603_1608Metric
R64, R65: 20k; R_0603_1608Metric
U1: AMS1117-3.3; SOT-223-3_TabPin2
U2: DRV8301; HTSSOP-56-1EP_6.1x14mm_P0.5mm_EP3.61x6.35mm
U3: TP2604-SR; SOIC-8_3.9x4.9mm_P1.27mm

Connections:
+5V: C7.2, C19.2, C20.2, C21.2, C22.2, L1.2, R21.1, U1.3 (VI); also elsewhere on the board
/MCU/BR_SO1: C16.2, R26.1; also elsewhere on the board
/MCU/BR_SO2: C57.2, R28.1; also elsewhere on the board
/MCU/BR_SO3: C58.2, R30.1; also elsewhere on the board
/MCU/CS: U2.8 (nSCS); also elsewhere on the board
/MCU/EN_GATE: R25.1, U2.16 (EN_GATE); also elsewhere on the board
/MCU/FAULT: R22.2, U2.6 (FAULT); also elsewhere on the board
/MCU/H1: U2.17 (INH_A); also elsewhere on the board
/MCU/H2: U2.19 (INH_B); also elsewhere on the board
/MCU/H3: U2.21 (INH_C); also elsewhere on the board
/MCU/L1: U2.18 (INL_A); also elsewhere on the board
/MCU/L2: U2.20 (INL_B); also elsewhere on the board
/MCU/L3: U2.22 (INL_C); also elsewhere on the board
/MCU/SDI: U2.9 (SDI); also elsewhere on the board
/MCU/SDO: R24.1, U2.10 (SDO); also elsewhere on the board
/MCU/SENS1: R27.2, R29.2; also elsewhere on the board
/MCU/SENS2: R31.2, R32.2; also elsewhere on the board
/MCU/SENS3: R36.2, R38.2; also elsewhere on the board
/MCU/SLCK: U2.11 (SCLK); also elsewhere on the board
/Mosfet driver/GH_A: U2.47 (GH_A); also elsewhere on the board
/Mosfet driver/GH_B: U2.42 (GH_B); also elsewhere on the board
/Mosfet driver/GH_C: U2.37 (GH_C); also elsewhere on the board
/Mosfet driver/GL_A: U2.45 (GL_A); also elsewhere on the board
/Mosfet driver/GL_B: U2.40 (GL_B); also elsewhere on the board
/Mosfet driver/H1_VS: C18.2, R27.1, U2.46 (SH_A); also elsewhere on the board
/Mosfet driver/H2_LOW: U2.39 (SL_B); also elsewhere on the board
/Mosfet driver/H2_VS: C24.2, R31.1, U2.41 (SH_B); also elsewhere on the board
/Mosfet driver/H3_LOW: U2.34 (SL_C); also elsewhere on the board
/Mosfet driver/H3_VS: C27.2, R36.1, U2.36 (SH_C); also elsewhere on the board
unnamed: C12.2, R20.2
unnamed: C13.2, R20.1, U2.2 (COMP)
unnamed: C14.1, U2.56 (SS_TR)
unnamed: C17.1, U2.52 (BST_BK)
unnamed: C17.2, D6.1 (K), L1.1, U2.50 (PH), U2.51 (PH)
unnamed: C18.1, U2.48 (BST_A)
unnamed: C23.1, U2.15 (CP2)
unnamed: C23.2, U2.14 (CP1)
unnamed: C24.1, U2.43 (BST_B)
unnamed: C25.1, C26.1, U2.13 (GVDD)
unnamed: C27.1, U2.38 (BST_C)
unnamed: C28.1, U2.23 (DVDD)
unnamed: C30.2, U2.27 (AVDD)
unnamed: C59.1, R34.2, R35.1, U3.5 (+)
unnamed: J4.1 (A), U2.55 (EN_BUCK)
unnamed: R18.1, R21.2, U2.3 (VSENSE)
unnamed: R19.1, U2.1 (RT_CLK)
unnamed: R23.2, U2.7 (DTC)
unnamed: R26.2, U2.25 (S01)
unnamed: R28.2, U2.26 (S02)
unnamed: R30.2, R64.1, U3.1
unnamed: R64.2, R66.1, U3.2 (-)
unnamed: R65.1, U3.6 (-), U3.7
unnamed: R65.2, R67.1, U3.3 (+)
SNA: C29.2, U2.33 (SN2); also elsewhere on the board
SNB: C33.1, U2.31 (SN2); also elsewhere on the board
SNC: C34.1, R66.2; also elsewhere on the board
SPA: C29.1, U2.32 (SP1); also elsewhere on the board
SPB: C33.2, U2.30 (SP2); also elsewhere on the board
SPC: C34.2, R67.2; also elsewhere on the board
V_SUPPLY: C15.2, C31.2, U2.29 (PVDD1), U2.53 (PVDD2), U2.54 (PVDD2); also elsewhere on the board

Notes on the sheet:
3.3v regulator for the logic
Phase sense voltage dividers
Op Amp Current Sense for 3rd Phase

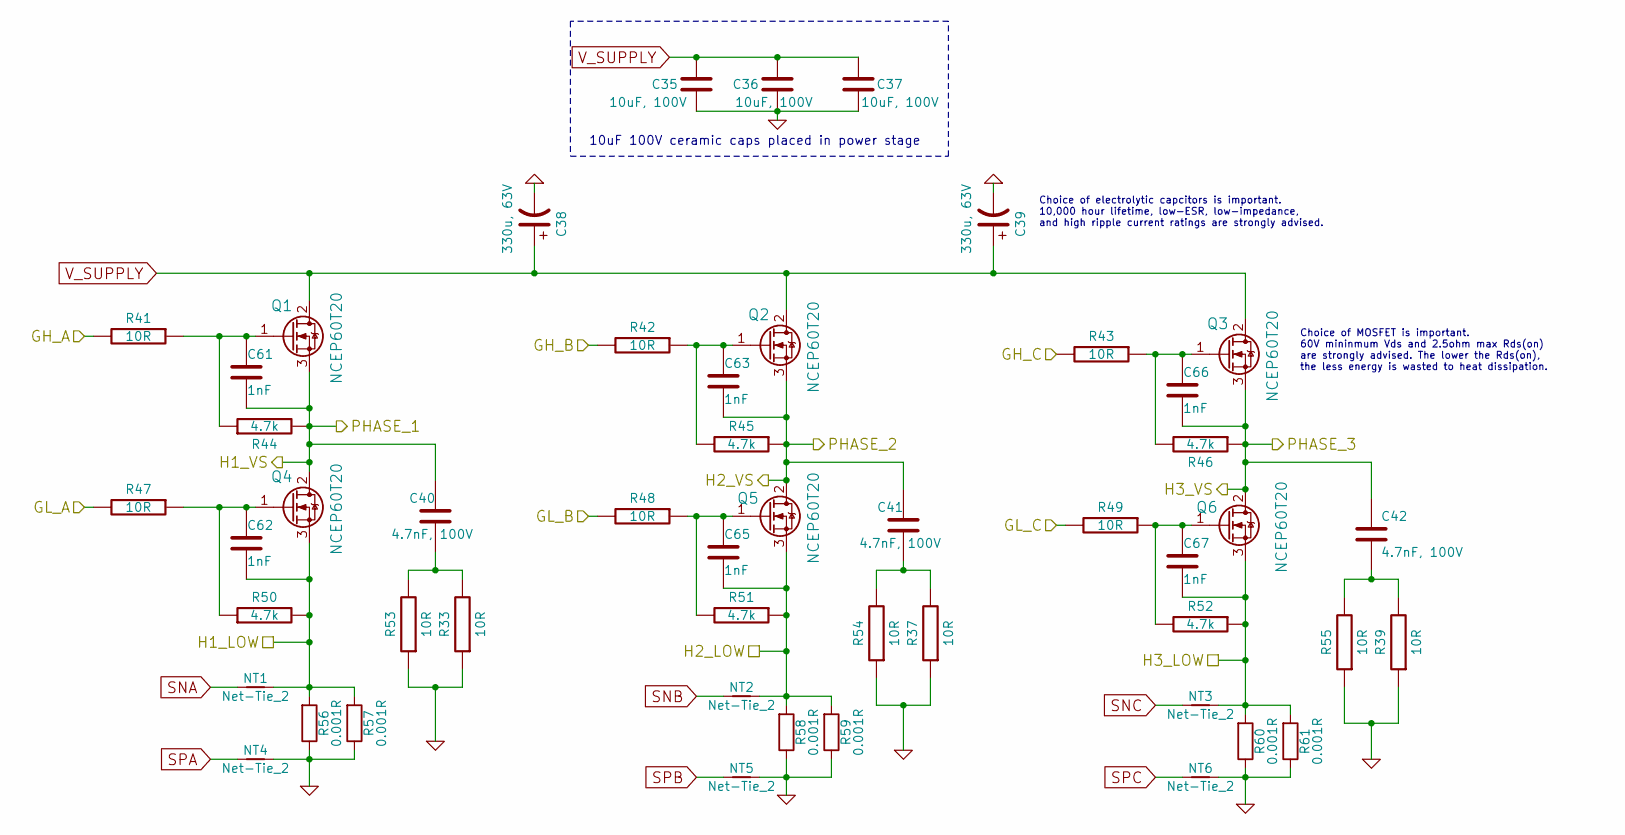
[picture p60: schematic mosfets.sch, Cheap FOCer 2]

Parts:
C35, C36, C37: 10uF, 100V; C_2220_5650Metric_Pad1.97x5.40mm_HandSolder
C38, C39: 330u, 63V; CP_10x20mm_hor_with_model_brd_edge
C40, C41, C42: 4.7nF, 100V; C_0805_2012Metric
C61, C62, C63, C65, C66, C67: 1nF; C_0603_1608Metric
NT1, NT2, NT3, NT4, NT5, NT6: Net-Tie_2; NetTie-2_SMD_Pad0.5mm
Q1, Q2, Q3, Q4, Q5, Q6: NCEP60T20; TO-220-3_Horizontal_TabUp_no_hole
R33, R37, R39, R41, R42, R43, R47, R48, R49, R53, R54, R55: 10R; R_0805_2012Metric
R44, R45, R46, R50, R51, R52: 4.7k; R_0603_1608Metric
R56, R57, R58, R59, R60, R61: 0.001R; R_2512_Yageo_big_pads

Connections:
/Mosfet driver/GH_A: R41.2; also elsewhere on the board
/Mosfet driver/GH_B: R42.2; also elsewhere on the board
/Mosfet driver/GH_C: R43.2; also elsewhere on the board
/Mosfet driver/GL_A: R47.2; also elsewhere on the board
/Mosfet driver/GL_B: R48.2; also elsewhere on the board
/Mosfet driver/H1_VS: C40.1, C61.2, Q1.3 (S), Q4.2 (D), R44.2; also elsewhere on the board
/Mosfet driver/H2_LOW: C65.2, NT2.2, Q5.3 (S), R51.1, R58.2, R59.2; also elsewhere on the board
/Mosfet driver/H2_VS: C41.1, C63.2, Q2.3 (S), Q5.2 (D), R45.1; also elsewhere on the board
/Mosfet driver/H3_LOW: C67.2, NT3.2, Q6.3 (S), R52.1, R60.2, R61.2; also elsewhere on the board
/Mosfet driver/H3_VS: C42.1, C66.2, Q3.3 (S), Q6.2 (D), R46.1; also elsewhere on the board
unnamed: C40.2, R33.2, R53.2
unnamed: C41.2, R37.2, R54.2
unnamed: C42.2, R39.2, R55.2
unnamed: C61.1, Q1.1 (G), R41.1, R44.1
unnamed: C63.1, Q2.1 (G), R42.1, R45.2
unnamed: C65.1, Q5.1 (G), R48.1, R51.2
unnamed: C66.1, Q3.1 (G), R43.1, R46.2
SNA: NT1.1; also elsewhere on the board
SNB: NT2.1; also elsewhere on the board
SNC: NT3.1; also elsewhere on the board
SPA: NT4.1; also elsewhere on the board
SPB: NT5.1; also elsewhere on the board
SPC: NT6.1; also elsewhere on the board
V_SUPPLY: C35.2, C36.2, C37.2, C38.1, C39.1, Q1.2 (D), Q2.2 (D), Q3.2 (D); also elsewhere on the board

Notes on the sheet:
10uF 100V ceramic caps placed in power stage
Choice of electrolytic capcitors is important. 10,000 hour lifetime, low-ESR, low-impedance, and high ripple current ratings are strongly advised.
Choice of MOSFET is important. 60V mininmum Vds and 2.5ohm max Rds(on) are strongly advised. The lower the Rds(on), the less energy is wasted to heat dissipation.

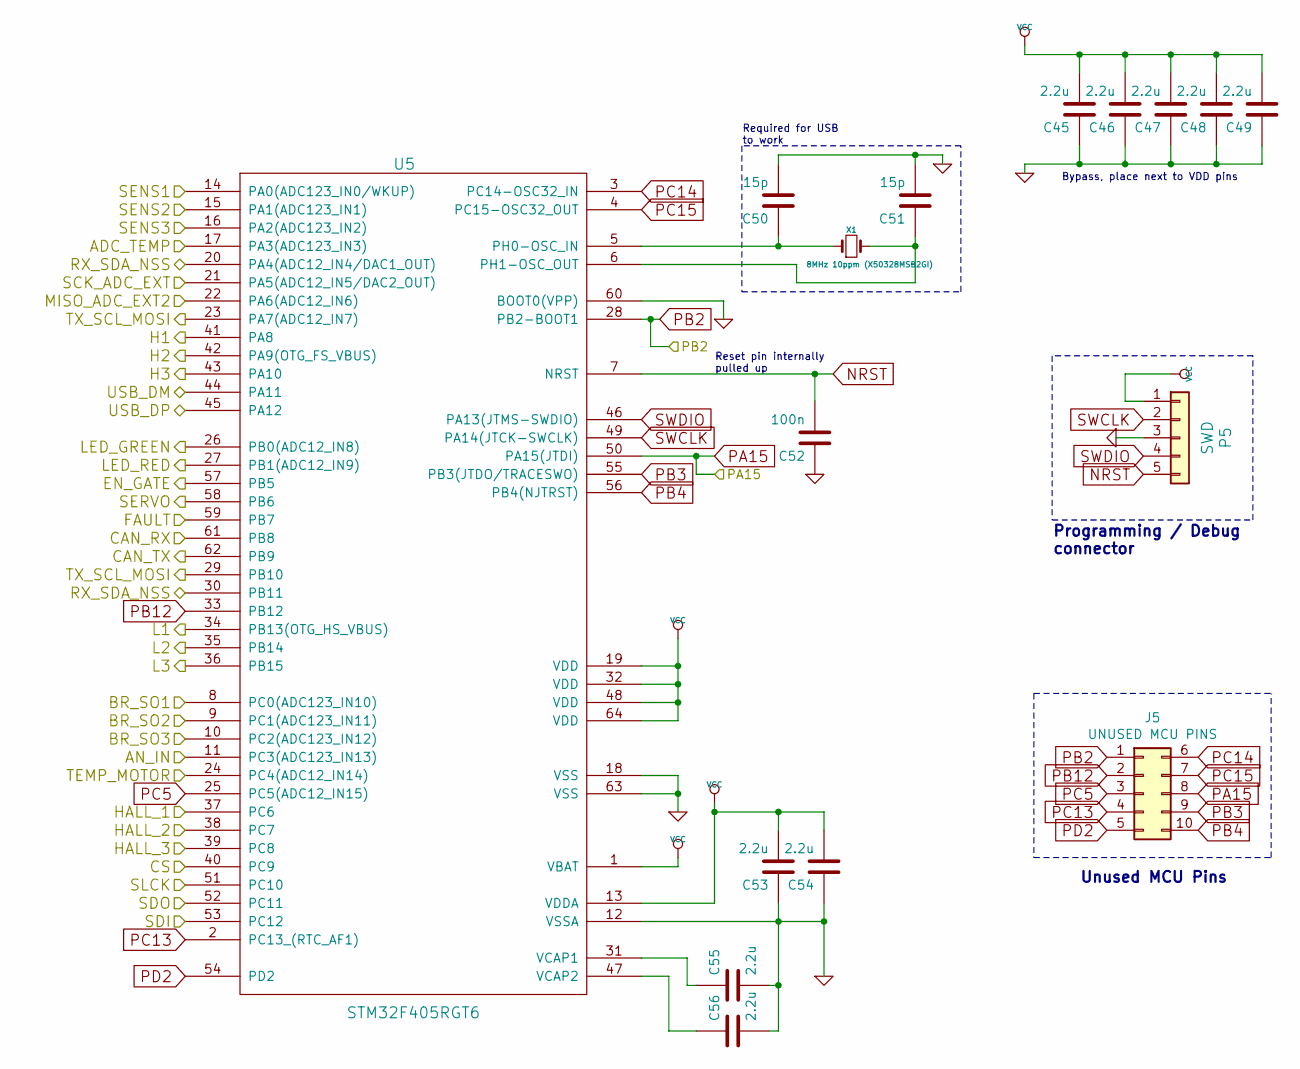
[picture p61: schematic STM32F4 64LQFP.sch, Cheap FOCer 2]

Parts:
C45, C46, C47, C48, C49, C53, C54, C55, C56: 2.2u; C_0603_1608Metric
C50, C51: 15p; C_0603_1608Metric
C52: 100n; C_0603_1608Metric
J5: UNUSED MCU PINS; PinHeader_2x05_P2.00mm_Vertical
P5: SWD; PinHeader_1x05_P2.54mm_Vertical
U5: STM32F405RGT6; LQFP-64_10x10mm_P0.5mm
X1: 8MHz 10ppm (X50328MSB2GI); Crystal_SMD_5032-2Pin_5.0x3.2mm; mfg# ABM3B-8.0-10-1UT

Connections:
/CAN bus transceiver/CAN_RX: U5.61 (PB8); also elsewhere on the board
/CAN bus transceiver/CAN_TX: U5.62 (PB9); also elsewhere on the board
/Filters/HALL1_IN: U5.37 (PC6); also elsewhere on the board
/Filters/HALL2_IN: U5.38 (PC7); also elsewhere on the board
/Filters/TEMP_IN: U5.24 (PC4(ADC12_IN14)); also elsewhere on the board
/HALL3: U5.39 (PC8); also elsewhere on the board
/MCU/ADC_TEMP: U5.17 (PA3(ADC123_IN3)); also elsewhere on the board
/MCU/AN_IN: U5.11 (PC3(ADC123_IN13)); also elsewhere on the board
/MCU/BR_SO1: U5.8 (PC0(ADC123_IN10)); also elsewhere on the board
/MCU/BR_SO2: U5.9 (PC1(ADC123_IN11)); also elsewhere on the board
/MCU/BR_SO3: U5.10 (PC2(ADC123_IN12)); also elsewhere on the board
/MCU/CS: U5.40 (PC9); also elsewhere on the board
/MCU/EN_GATE: U5.57 (PB5); also elsewhere on the board
/MCU/FAULT: U5.59 (PB7); also elsewhere on the board
/MCU/H1: U5.41 (PA8); also elsewhere on the board
/MCU/H2: U5.42 (PA9(OTG_FS_VBUS)); also elsewhere on the board
/MCU/H3: U5.43 (PA10); also elsewhere on the board
/MCU/L1: U5.34 (PB13(OTG_HS_VBUS)); also elsewhere on the board
/MCU/L2: U5.35 (PB14); also elsewhere on the board
/MCU/L3: U5.36 (PB15); also elsewhere on the board
/MCU/LED_GREEN: U5.26 (PB0(ADC12_IN8)); also elsewhere on the board
/MCU/LED_RED: U5.27 (PB1(ADC12_IN9)); also elsewhere on the board
/MCU/MISO_ADC_EXT2: U5.22 (PA6(ADC12_IN6)); also elsewhere on the board
/MCU/RX_SDA_NSS: U5.20 (PA4(ADC12_IN4/DAC1_OUT)), U5.30 (PB11); also elsewhere on the board
/MCU/SCK_ADC_EXT: U5.21 (PA5(ADC12_IN5/DAC2_OUT)); also elsewhere on the board
/MCU/SDI: U5.53 (PC12); also elsewhere on the board
/MCU/SDO: U5.52 (PC11); also elsewhere on the board
/MCU/SENS1: U5.14 (PA0(ADC123_IN0/WKUP)); also elsewhere on the board
/MCU/SENS2: U5.15 (PA1(ADC123_IN1)); also elsewhere on the board
/MCU/SENS3: U5.16 (PA2(ADC123_IN2)); also elsewhere on the board
/MCU/SERVO: U5.58 (PB6); also elsewhere on the board
/MCU/SLCK: U5.51 (PC10); also elsewhere on the board
/MCU/TX_SCL_MOSI: U5.23 (PA7(ADC12_IN7)), U5.29 (PB10); also elsewhere on the board
/MCU/USB_DM: U5.44 (PA11); also elsewhere on the board
/MCU/USB_DP: U5.45 (PA12); also elsewhere on the board
NRST: C52.2, P5.5, U5.7 (NRST)
unnamed: C50.1, U5.5 (PH0-OSC_IN), X1.1
unnamed: C51.1, U5.6 (PH1-OSC_OUT), X1.2
unnamed: C55.1, U5.31 (VCAP1)
unnamed: C56.1, U5.47 (VCAP2)
PB3: J5.9, U5.55 (PB3(JTDO/TRACESWO))
PB4: J5.10, U5.56 (PB4(NJTRST))
PB12: J5.2, U5.33 (PB12)
PC5: J5.3, U5.25 (PC5(ADC12_IN15))
PC13: J5.4, U5.2 (PC13_(RTC_AF1))
PC14: J5.6, U5.3 (PC14-OSC32_IN)
PC15: J5.7, U5.4 (PC15-OSC32_OUT)
PD2: J5.5, U5.54 (PD2)
SWCLK: P5.2, U5.49 (PA14(JTCK-SWCLK))
SWDIO: P5.4, U5.46 (PA13(JTMS-SWDIO))

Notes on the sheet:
Reset pin internally pulled up
Required for USB to work
Bypass, place next to VDD pins
Programming / Debug connector
Unused MCU Pins

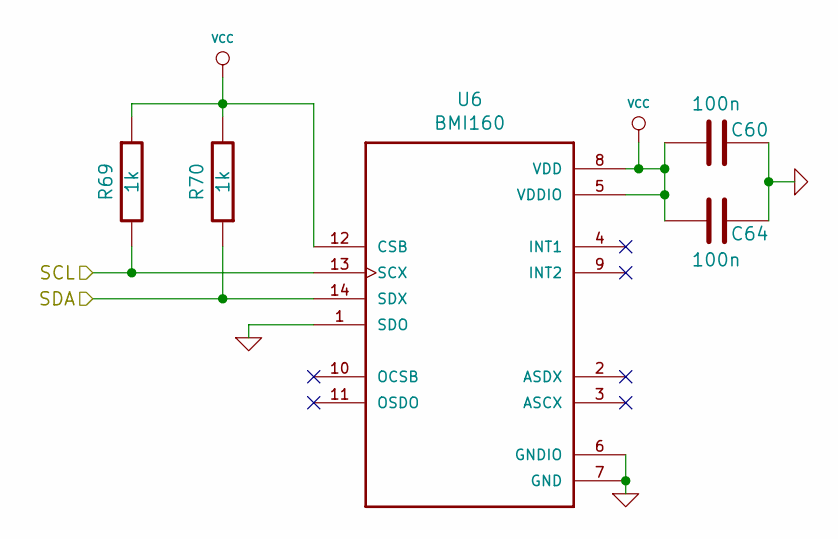
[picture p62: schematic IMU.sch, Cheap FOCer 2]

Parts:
C60, C64: 100n; C_0603_1608Metric
R49, R50: 1k; R_0603_1608Metric
U6: BMI160; Bosch_LGA-14_3x2.5mm_P0.5mm

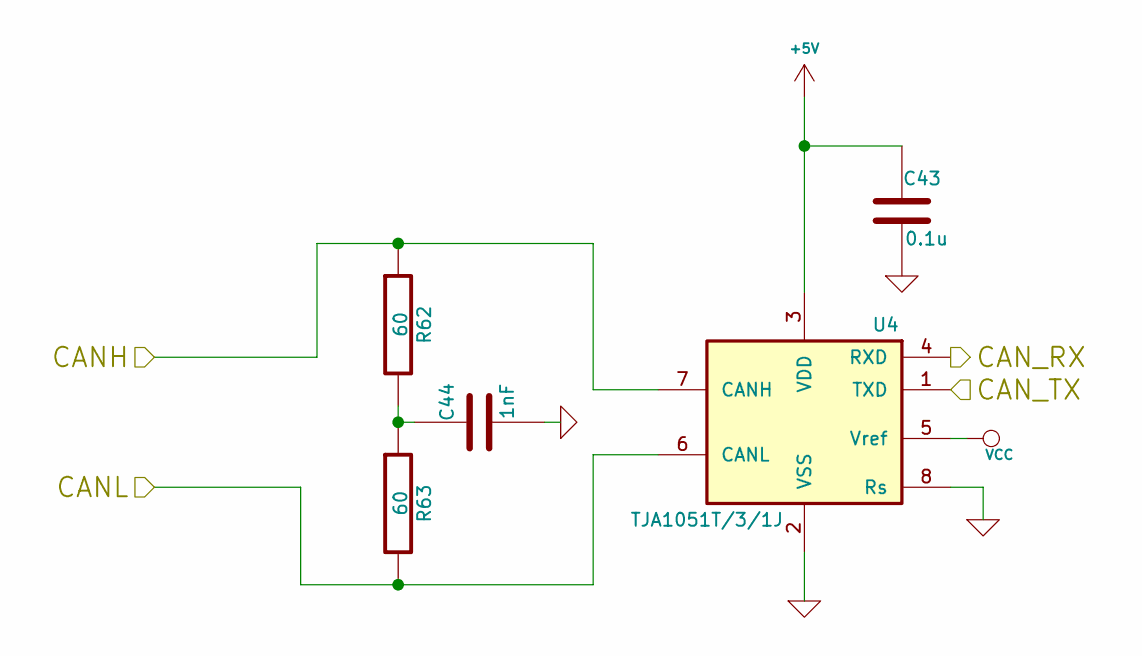
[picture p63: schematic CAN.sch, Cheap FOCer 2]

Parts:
C43: 0.1u; C_0603_1608Metric
C44: 1nF; C_0603_1608Metric
R62, R63: 60; R_0603_1608Metric
U4: TJA1051T/3/1J; SOIC-8_3.9x4.9mm_P1.27mm

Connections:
+5V: C43.1, U4.3 (VDD); also elsewhere on the board
/CAN bus transceiver/CANH: R62.1, U4.7 (CANH); also elsewhere on the board
/CAN bus transceiver/CANL: R63.2, U4.6 (CANL); also elsewhere on the board
/CAN bus transceiver/CAN_RX: U4.4 (RXD); also elsewhere on the board
/CAN bus transceiver/CAN_TX: U4.1 (TXD); also elsewhere on the board
unnamed: C44.1, R62.2, R63.1

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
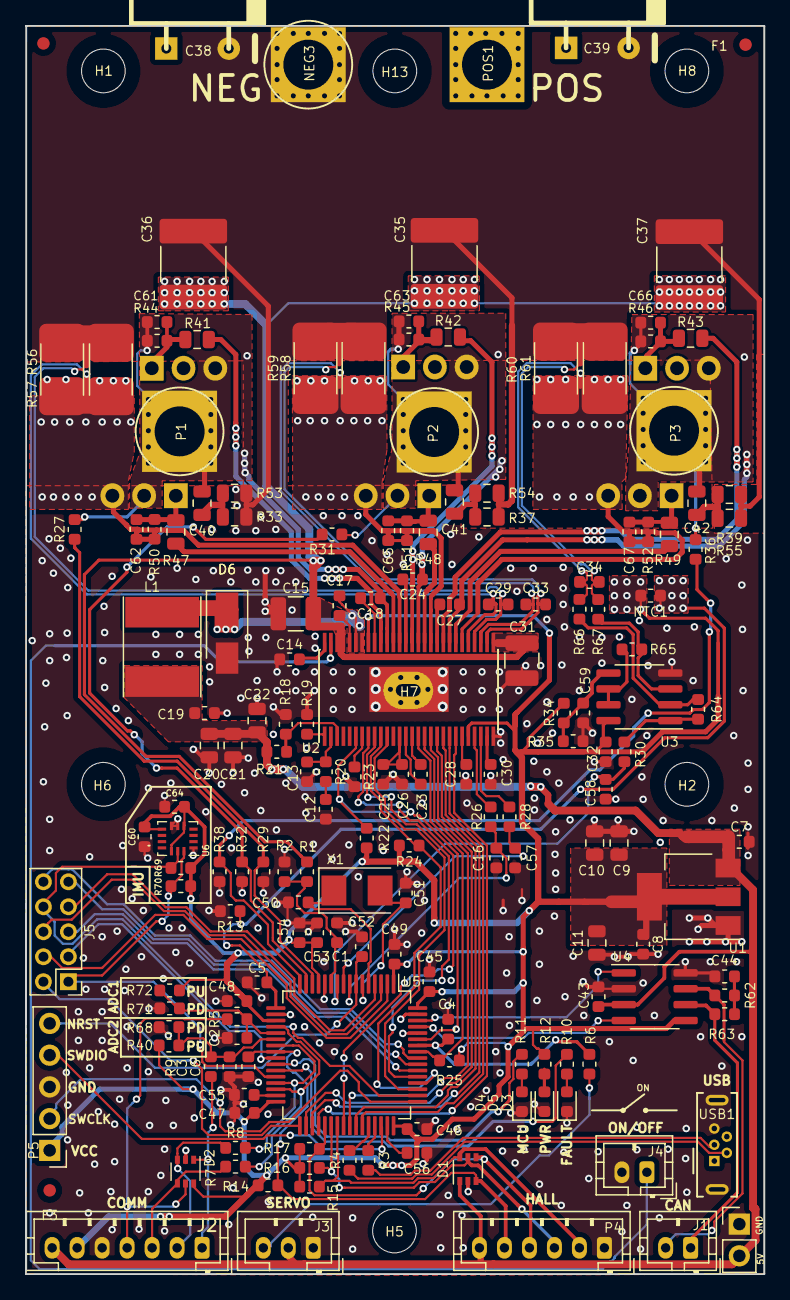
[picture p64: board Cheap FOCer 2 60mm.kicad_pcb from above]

Board: 2 copper layers, 59.1 x 99.9 mm, 193 parts (0 on the bottom side), 120 nets.

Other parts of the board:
R69, R70: 1k; R_0603_1608Metric

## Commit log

2020-04-14 Adding desgin files
    Adding desgin files
    [BLDC_4-2018-12-23-16-33-14.sch, BLDC_4-2018-12-23-16-59-10.sch, BLDC_4-2018-12-23-17-20-44.sch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]
2020-04-17 updating guides
    Added JLCPCB and LCSC ordering guides
    [JLCPCB BOM Cheap FOCer 2.xlsx, LCSC BOM Cheap FOCer 2.xlsx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]
2020-04-18 move Gerber file to root
    easier to find important files
2020-04-18 convert ordering guide to markdown
    easier to make and track changes
2020-04-18 move order instructions and support thread to top
2020-04-18 rename case insensitive git fs gerber.zip
2020-04-18 move bom file to root directory
    [bom.xlsx]
2020-04-18 move cpl file to root
    [cpl.csv]
2020-04-18 move bom lcsc file
    [bomLcsc.xlsx]
2020-04-18 update lcsc boom so that it is easier to use
    [bomLcsc.csv, bomLcsc.xlsx]
2020-04-18 add 5xbom csv
    [5XBomLcsc.csv, bomLcsc.csv]
2020-04-19 correct quantities for bxb connectors
    [5XBomLcsc.csv]
2020-04-19 convert bom.xls to csv
    [bom.csv, bom.xlsx]
2020-04-19 remove unused columns and update smnr quanty
    [5XBomLcsc.csv]
2020-04-20 missing )
    [5XBomLcsc.csv]
2020-04-20 add usb port
    [5XBomLcsc.csv]
2020-04-21 Update partsList.md
    @shamansystems how tall is the pcb with a heat sink? Guessing about 25mm to 30mm.
2020-04-21 add pin headers to parts list
2020-04-21 how to solder tiny things
2020-04-21 Update partsList.md
    Added solder recommendation
2020-04-22 Create Cheap FOCer 2 assembly Guide.docx
2020-04-22 Add black wire Ali link
2020-04-22 remove black/red wire link
2020-04-22 wip assembly guide md
2020-04-24 Update partsList.md
    only the 2.54mm 5-pin header is used for initial programming of the CFOC2 with an STlink.
2020-04-24 add pin headers to bom
    @shamansystems check it out yo
    [5XBomLcsc.csv]
2020-04-24 notes regarding diode and cap pols
2020-04-24 kicad how to open
2020-04-24 note regarding first timers
2020-04-24 wip heat sink assembly
2020-04-24 wip marking down the assembly guide
2020-04-25 rename heatSinkAssembly image
2020-04-25 add thread lock to parts
2020-04-25 add 12v power adapter
2020-04-25 power adapter
2020-04-25 rename pcb image
2020-04-28 Adding Firmware and VESC Tool
2020-04-29 note resistor solder bridges
2020-04-29 note regarding heat shrink for the pcb
    @shamansystems
2020-04-30 organize folders
    [BLDC_4-2018-12-23-16-33-14.sch, BLDC_4-2018-12-23-16-59-10.sch, BLDC_4-2018-12-23-17-20-44.sch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]
2020-04-30 wip lowerCase folder names
    [BLDC_4-2018-12-23-16-33-14.sch, BLDC_4-2018-12-23-16-59-10.sch, BLDC_4-2018-12-23-17-20-44.sch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]
2020-04-30 rename fo rizzle
    [BLDC_4-2018-12-23-16-33-14.sch, BLDC_4-2018-12-23-16-59-10.sch, BLDC_4-2018-12-23-17-20-44.sch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]
2020-05-04 change screw image
2020-05-04 Add case, change screws
2020-05-04 Fix screw name, and screw/washer/spacer quantity
2020-05-20 adding source and bootloader
    [pi_stm32.cfg, stm32-bv_openocd.cfg]
2020-05-23 Replace discontinued 6 pin header.
    [bom.csv]

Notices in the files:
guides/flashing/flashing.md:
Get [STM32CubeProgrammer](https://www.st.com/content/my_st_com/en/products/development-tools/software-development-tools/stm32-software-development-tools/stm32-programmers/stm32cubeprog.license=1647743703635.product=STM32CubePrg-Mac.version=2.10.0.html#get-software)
